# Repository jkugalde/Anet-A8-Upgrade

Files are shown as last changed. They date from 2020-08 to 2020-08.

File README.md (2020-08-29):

# Anet A8 Upgrade

I have an Anet A8, it was the cheapest 3d printer in the market around the time that i bought it (2019) and served its purpose well enough, but now with the pandemic lockdown i have enough time to invest in get some major upgrades done. 

This is a work in progress and i currently have only modified the frame, from acrylic to aluminium. I am planning to change the controller to one of the latest with touch screen compatibility, to make and enclosure to reduce heat dissipation and noise and maybe modify the mechanical arrangement to a corexy or something like that.

This is what i currently have:

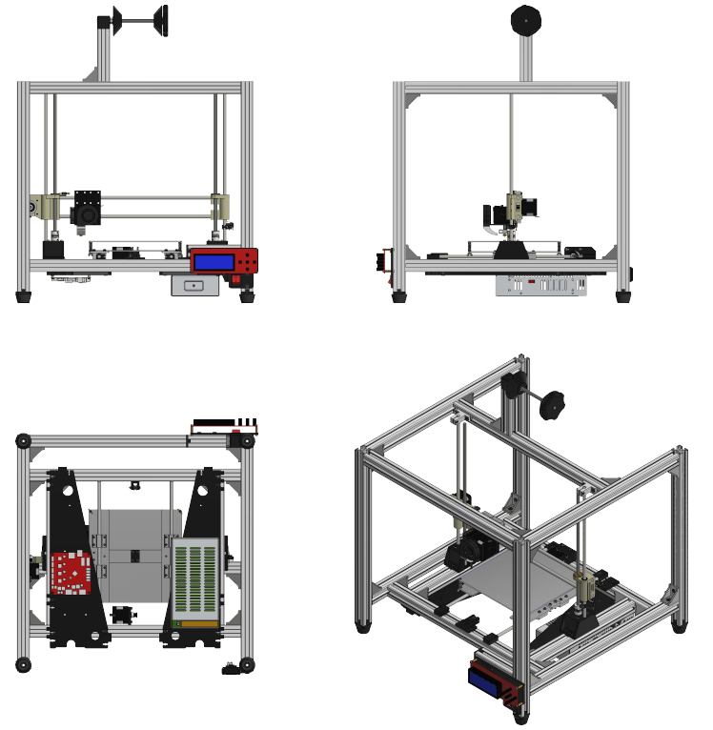
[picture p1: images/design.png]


# Design

The first objective in the project is to build a stiffer frame that is easy to enclose without invest too much time in making new parts to get the printer working, as it will be done anyway in the future when changing the controller and mechanical principle. 

## Aluminium frame

One of the main weaknesses of the AnetA8 is the acrylyc frame, which is not rigid enough to withstand high speed/torque, brittle, and difficult to enclose. As i had a good time making a [table](https://github.com/jkugalde/T-Slot-Table) with T-Slots aluminium profiles i thought why not?.

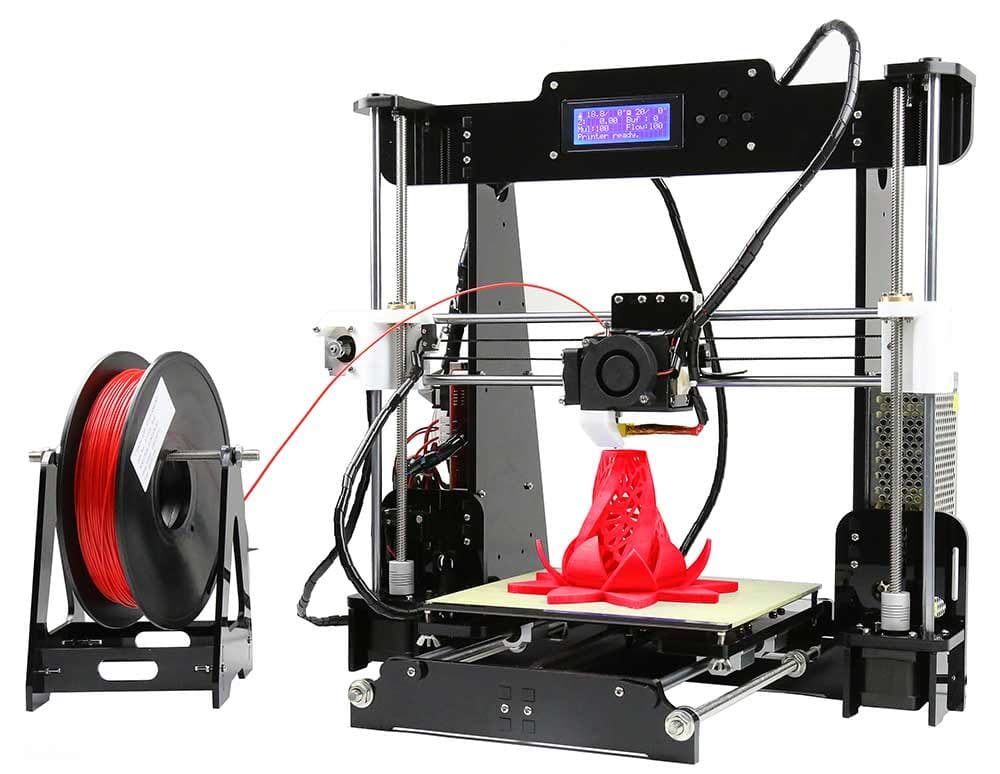
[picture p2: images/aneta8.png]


The criteria were:

- To make a box so it would be easier to build and enclose (probably more expensive tho).
- Big enough to fit the Anet parts.
- To use the profiles without cutting them.

I decided to use 30x30 T-Slots as they are cheaper and stronger than 20x20 V-Slots, which are also a good option to make machines too as there are plenty of accesories and also works as transmission system, but i am not going to make any changes in that last topic yet.

As the beams are sold in multiples of 250 mm and the Anet axis are longer than that i chose to use 500 mm profiles in the following design:

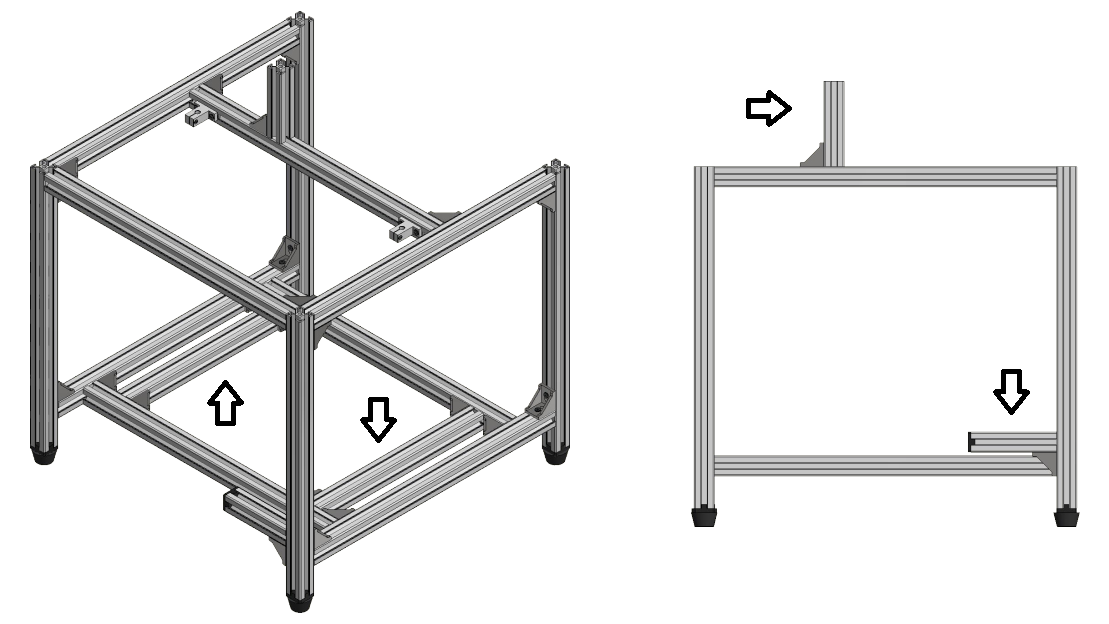
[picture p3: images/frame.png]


There is some space in the bottom to separate the electronics and power from the rest of the machine, wich will be in an enclosure in the future. The joints are corner brackets, you can add more or other type of joints to increase stiffness, i used the minimum as the enclosure will also help. The z axis rods are held by SK vertical supports. Unfortunately, there are four of the beams that must be cut to a different length, one of them is to hold the spool, other one for the screen, and the other two will support the z motors and define the length of the y axis. 

I could have made the y axis longer by simply not cutting these pair of profiles, but then i will have to buy new 8 mm steel rods, belt and bed system, so nah. I am planning to make a corexy anyway. Fortunately, i had a 1.5 m aluminium profile that i did not use in my table, so i cut it to make these beams and an extra 500 mm.

The foots are standard 30x30 T-Slot rubber foots with a 3d printed piece for attachment to the beams.

Finally, these are the parts:

Item                     | Quantity
 ---------------------------   | ------------
T-Slot 30x30x500 mm | 12
T-Slot 30x30x340 mm | 2
T-SLot 30x30x120 mm | 2
SK8 shaft support seat | 2
Corner bracket | 22
Rubber foots | 4
End Cap foot attachment | 5

NOTE1: The extra printed attachment is to cover the sharp corners of the aluminium profile that hols the screen.

NOTE2: The small beams could be smaller, like 3 cm smaller.

NOTE3: That extra beam for the LCD is temporal, as it will be held by the enclosure in the future.

## 3D Printed parts

As i dispose of the acrylyc frame, i had to design and print parts to hold and support some components. The idea was to make them small as possible until i get the printer working. The printed components are:

Item                     | Quantity
 ---------------------------   | ------------
Spool holder joint | 1
Spool holder nut hanlde | 1
Spool holder cone | 2
Y Axis rod holder A  | 2
Y Axis rod holder B  | 2
Y Axis pulley support | 1
Z Motor holder | 2
Y Motor holder  | 1
Z Endstop mount   | 1
Y Endstop mount   | 1
X Belt attachment| 2
Y Belt attachment A  | 1
Y Belt attachment B  | 1
Rocker Switch mount | 1
Power inlet mount | 1

The x belt attachments were made as the previous system (bolts and zip ties) is awful, these are not too fancy either, but will stand long enough until i change the extruder for something else.

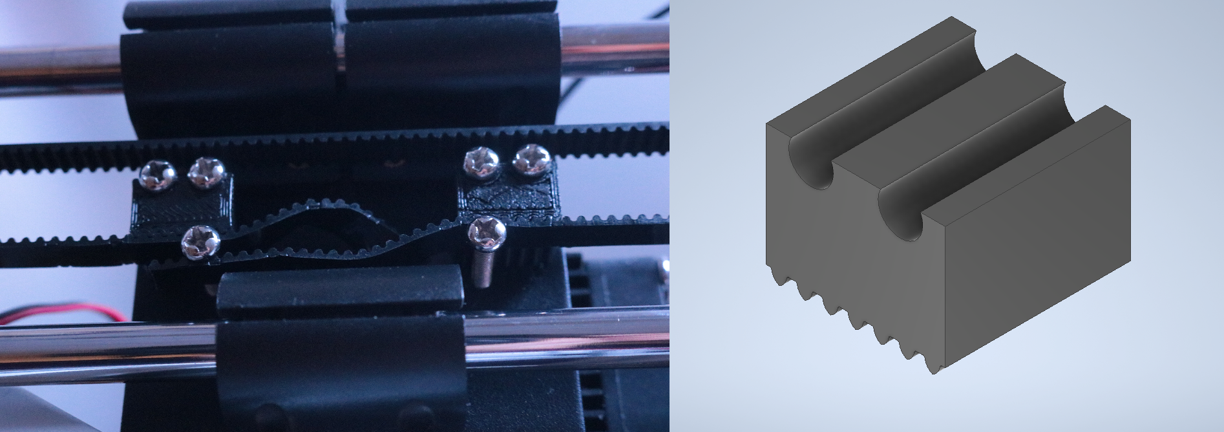
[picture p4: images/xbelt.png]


The y belt attachments were made as the height of the belt with respect to the y carriage changed. 

The other parts of the spool holder are on my [Thingiverse](https://www.thingiverse.com/thing:3457712), aswell as in this repository, except for the piece that joint the spool holder with the frame.

## Electronics

To hold the electronics the idea is to add a sheet of acrylic with mounting holes in the bottom face of the frame, but that will be done with the rest of the enclosure, so for now i will use the original parts of the anet where the electronics is mounted on, which attach really fine to the T-Slots and make everything easier, except for the inaccesibility of the SD port... well, is not difficult to make new holes to put the board closer to the edge or just USB print meanwhile.

I also reused one of the acrylic panels to hold the LCD.

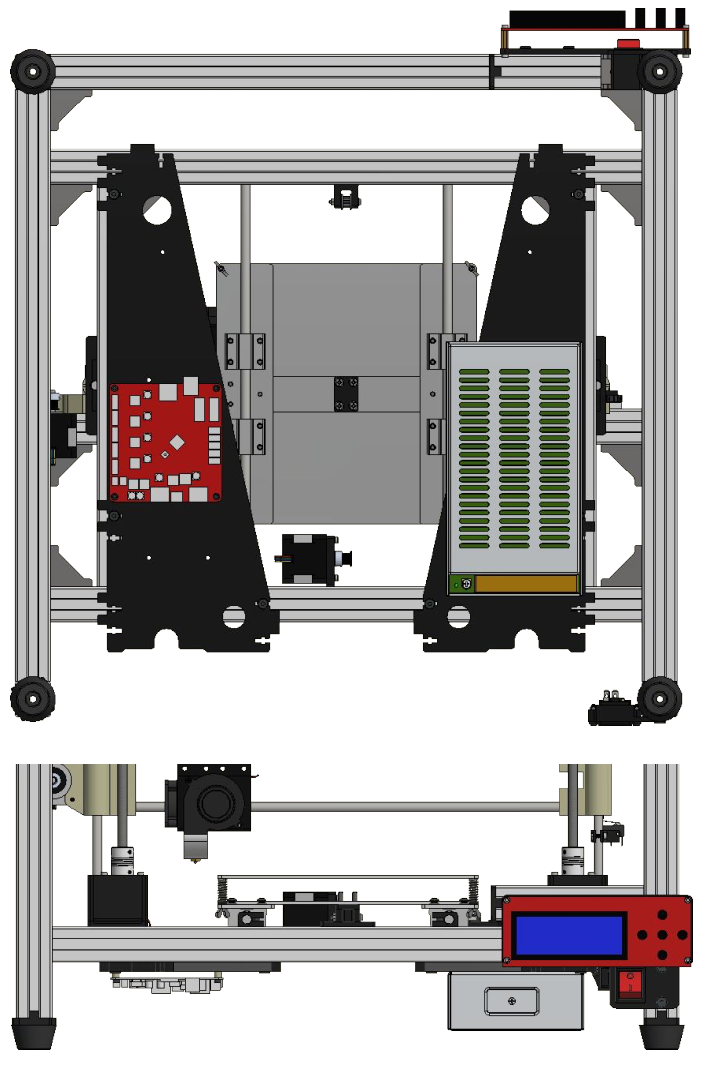
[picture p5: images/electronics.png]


# Manufacturing

## Disassembly

All the acrylyc frame was dispossed with the exception of the panels mentioned before.

All the other important parts were used, but the bearings that tightens the y belt were replaced with a proper GT2-16 idle pulley, which is also a good idea for the x belt, but there is not enough room.

## Cutting the profiles

I cut the 1.5 m profile with saw and then rectified the faces using a Tormach. The length has to be as accurate as possible and the faces must be flat to get a decent joint.

## Printing

All the part were printed with 0.3 mm layer height, 3 shells and 30% infill, no support nor raft, with exception of the z motor holders. These are the orientations:

Drill bits with the right dimensions were passed through all the holes in the pieces once they were printed, to clean.

## Extending wires

Some of the wires had to be extended due to the new position of the controller, these were:

- X endstop
- Extruder motor, fans, thermistor, heat cartridge
- Z endstop.

I had a power socket previously installed in the printer with a rocker switch, if you want to do this you will have to wire it like this:

(image)

# Assembly

## Frame

To assemble the profiles it is necessary to have a good square set and flat surfaces to get the joints perpendicular. 

- The first step is to attach the corner brackets (not too tight until the end) into every profile with bolts (M5x12) and nuts, you can use other profiles to help you with. 

- Then, assemble the "sides"

- The inside. Use a caliper to get the distances right.

- Put the sides in the inside.

- The upper profiles.

- Finally, the spool holder, but you can put it after all the other steps so it doesnt bother when wiring.

Be sure that the bolts are tight.

## Y Axis

- The motor in its holder then into the frame. Attach the motor loosely to then use the slotholes to tighten the belt.

- The pulley support.

- Put the shafts in the bed carriage and then into the rod holders. 

- This assembly into the frame.

- The y endstop support.

- The belt in the attachment and around the pulleys, and then tighten with the motor holder slotholes.

## X Axis

- The belt attachments and bolt (loosely).

- The shafts faces must be aligned with this side of the right support.

- Put the belt through the bearings, the motor, and then into the attachments. Fasten the bolt.

## Z Axis

- Put the motors (with the couple) in the holders, also bolts and nuts to attach to the profile.

- Pass the shafts and ACME thread through the bearings and nut.

- Put the assembly on the motors, fasten the set screw on the couples.

- Attach the SK8 to the shafts and frame.

- Attach the z endstop support (loosely).

To align the x axis, you can move the gantry all the way up in the z axis and compare the amount of ACME thread coming up from the nut and adjust.

## Electronics

- Use M3 bolts to attach the power source to one of the large acrylic panels, put M5x8 bolts and nuts in the indicated positions (yes, they fit right in).

- Use M3 bolts and nut and plastic separators to attach the motherboard to the other acrylic panel. Put the M5 bolts in the same positions as the previous step.

- Attach them to the frame.

- Connect everything as it was.

The wires were wrapped around with spiral wire wrap tube.

## Done(?)

Remember to level the bed. In my printer i also have a glass bed from an Ender3.

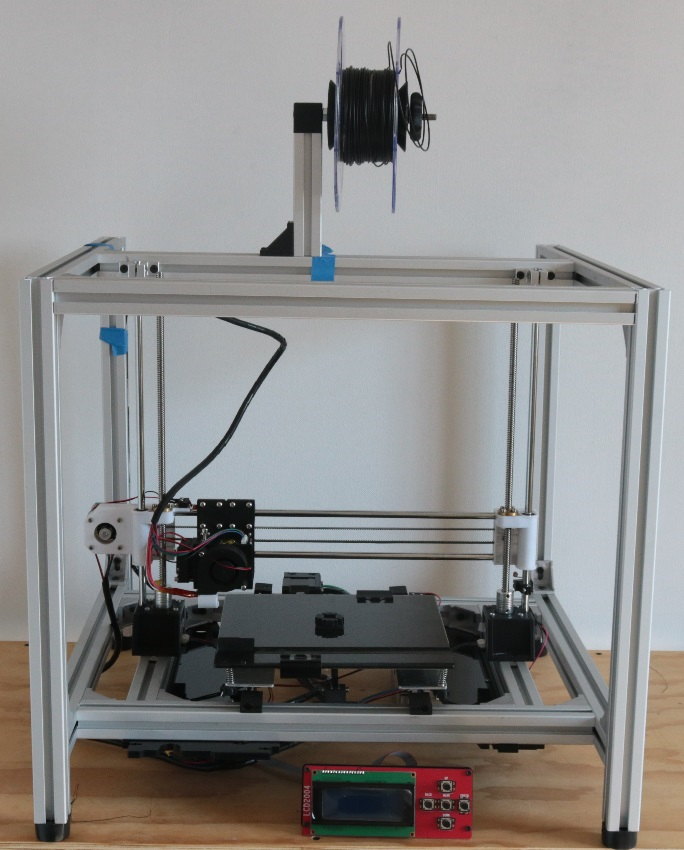
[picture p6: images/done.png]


# Further work

- Change the controller
- Build the enclosure
- Change the mechanical principle

With the current setting the usable printing area will 250x210 mm (X x Y) so it is a good idea to get a borosilicate glass bed to attach (remember to use only three bolts in the bed). There is a loss of Y space as i put the glass bed with metal clips, also because of the design, with other configuration you could get an extra 5-6 centimeters without the bed crashing into the enclosure.

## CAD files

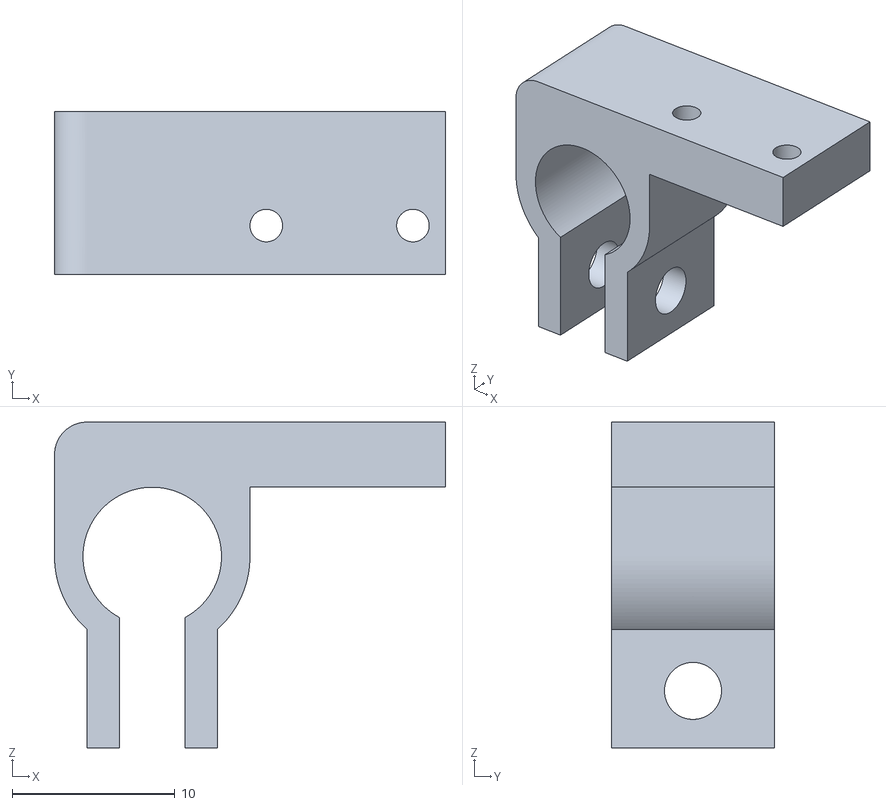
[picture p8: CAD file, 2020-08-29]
STLS/ZEndstopMount.stl
24.0 x 10.0 x 20.0

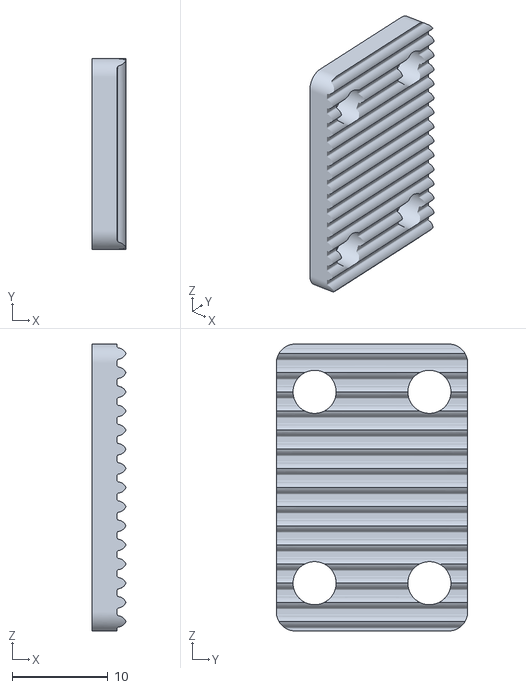
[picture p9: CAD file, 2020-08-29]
STLS/Y belt attachment B.stl
3.55 x 20.0 x 30.0

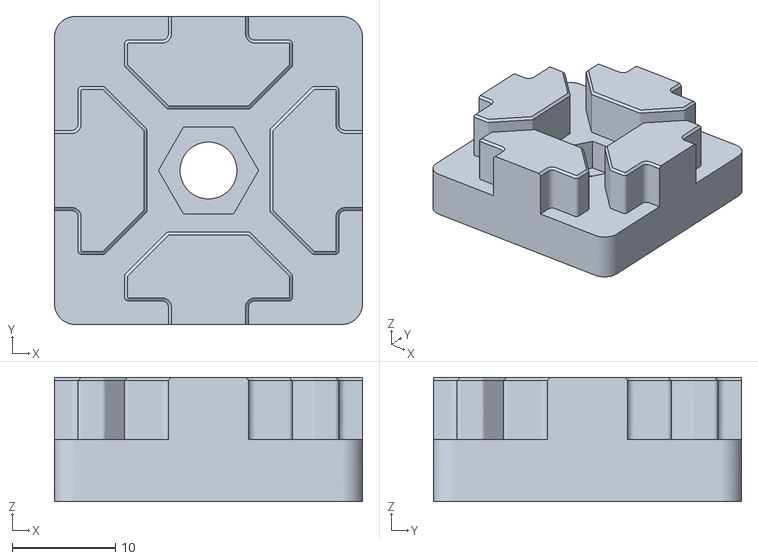
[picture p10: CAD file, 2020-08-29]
STLS/EndCapFoot.stl
29.8 x 29.8 x 12.0

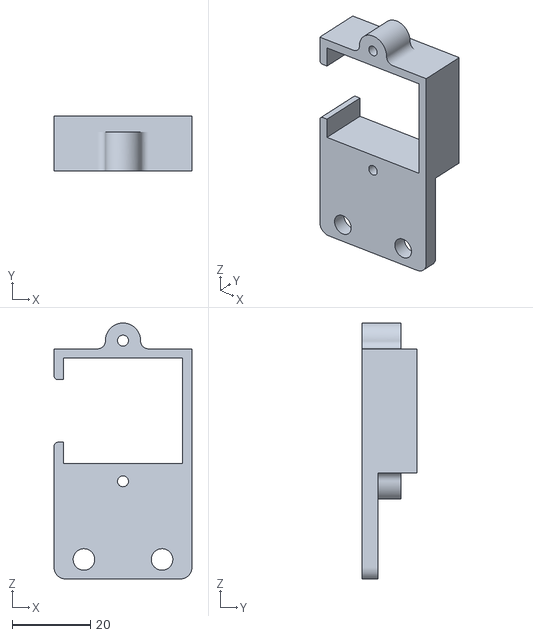
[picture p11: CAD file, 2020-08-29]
STLS/SocketMount.stl
35.3 x 14.0 x 65.5

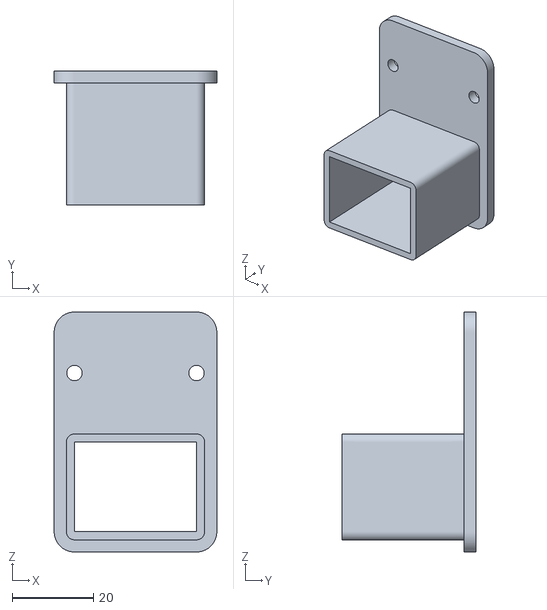
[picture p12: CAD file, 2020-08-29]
STLS/ButtonBox.stl
40.0 x 33.0 x 59.0

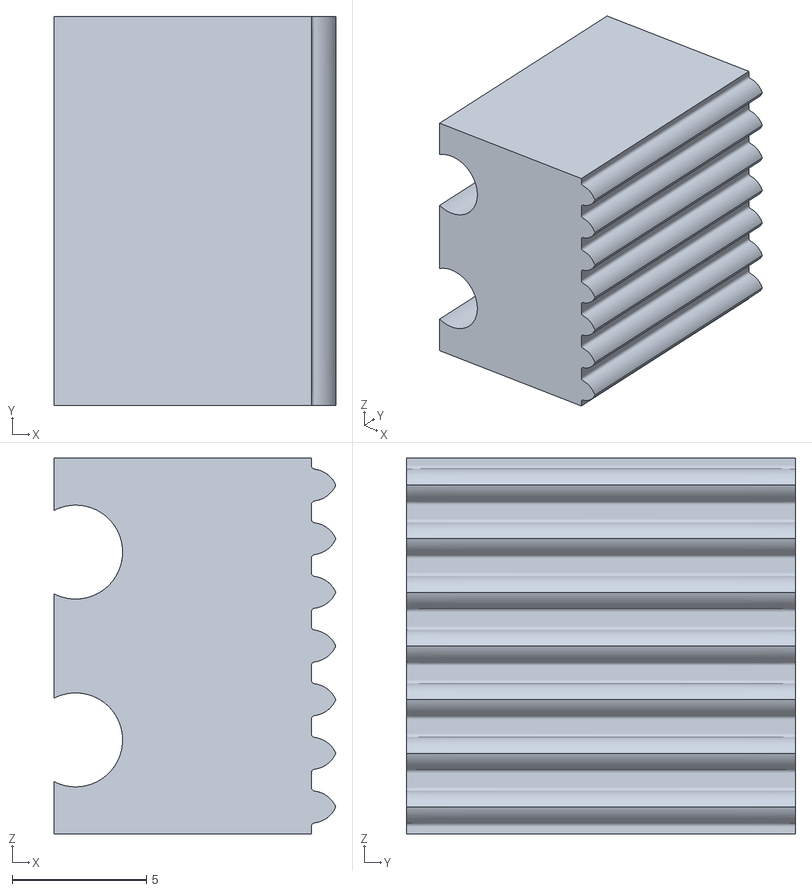
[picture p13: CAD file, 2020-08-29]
STLS/XBeltPress.stl
10.5 x 14.5 x 14.0

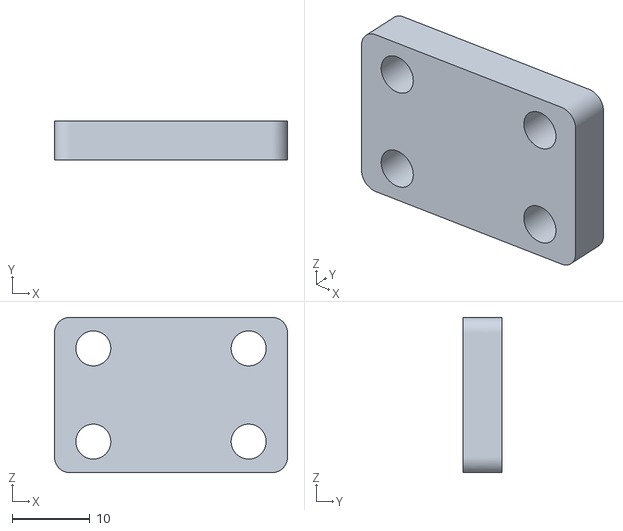
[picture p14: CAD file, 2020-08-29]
STLS/Y belt attachment A.stl
30.0 x 5.00 x 20.0

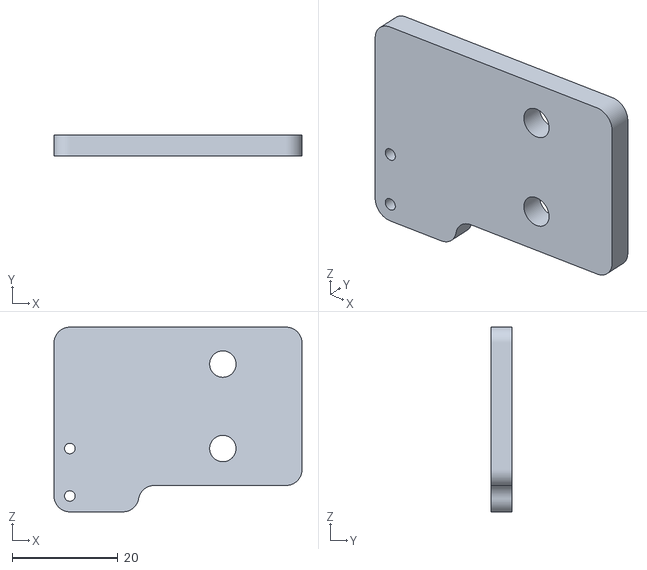
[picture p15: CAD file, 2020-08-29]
STLS/YEndstopMount.stl
47.0 x 4.00 x 35.0

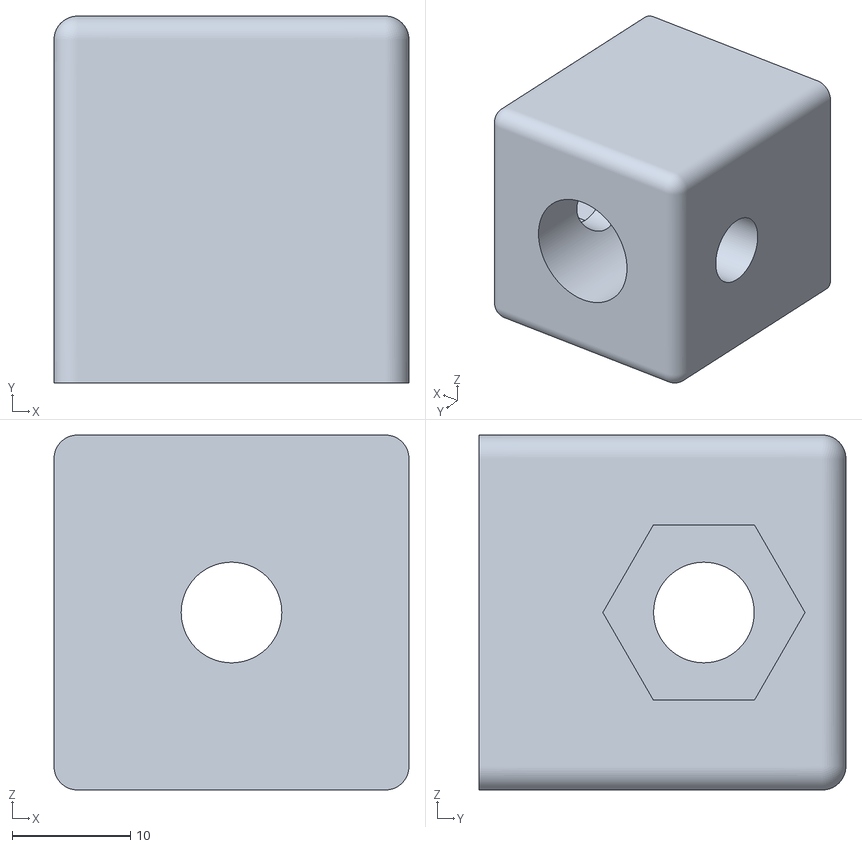
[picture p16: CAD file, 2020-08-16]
STLS/SpoolHolderJoint.stl
30.0 x 31.0 x 30.0

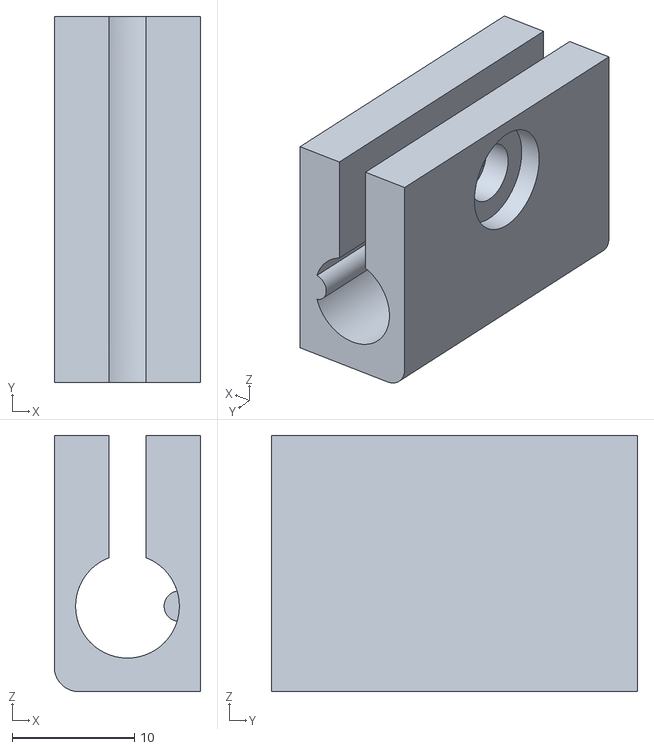
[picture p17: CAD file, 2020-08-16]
STLS/YsupportA.stl
12.0 x 30.0 x 21.0

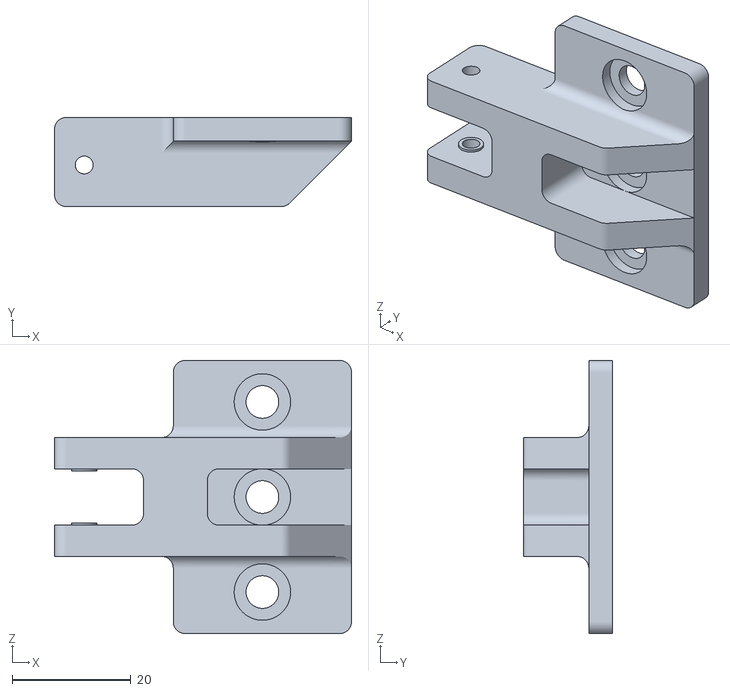
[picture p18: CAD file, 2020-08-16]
STLS/PulleySupport.stl
50.0 x 15.0 x 46.0

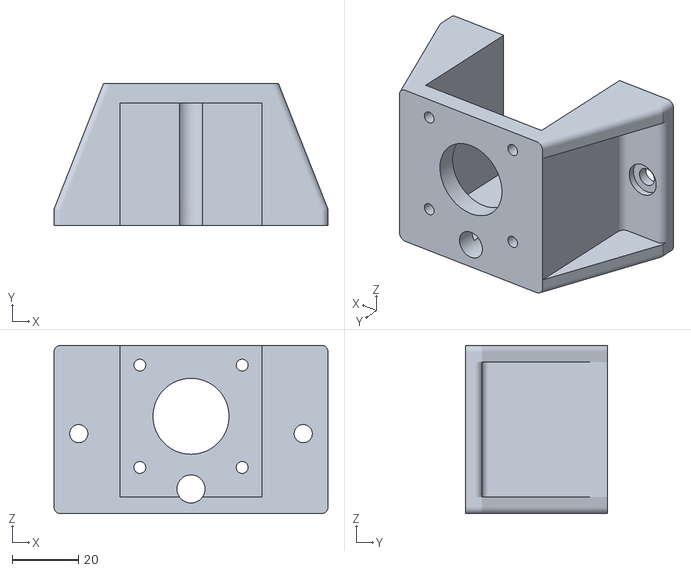
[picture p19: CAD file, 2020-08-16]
STLS/ZMotorSupport.stl
83.0 x 43.1 x 51.0

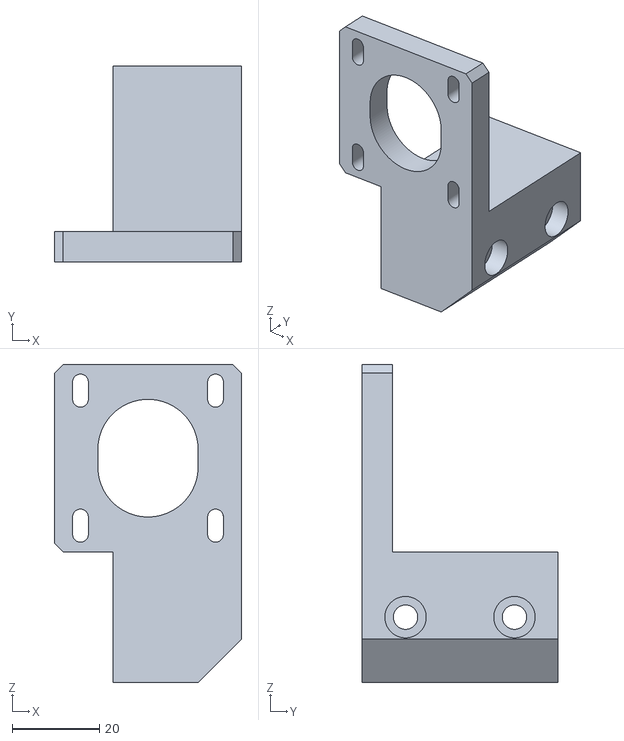
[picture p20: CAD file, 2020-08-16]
STLS/YMotorHolder.stl
43.0 x 45.0 x 73.0

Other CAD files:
STLS/YsupportB.stl
CAD/3030_endCap.ipt
CAD/3030cornerbracket.ipt
CAD/30x30x125.ipt
CAD/30x30x250.ipt
CAD/30x30x340.ipt
CAD/30x30x500.ipt
CAD/8x380axis.ipt
CAD/8x435axis.ipt
CAD/ACMENut.ipt
CAD/ACMEThread.ipt
CAD/AnetUpgrade.iam
CAD/Anet_A8_Main_Board_shell_v1.1.ipt
CAD/Bearing Ball, GT2 Timing Idler Pulley, Configurable_1 mm.ipt
CAD/Bearing Inner Ring, GT2 Timing Idler Pulley, Configurable_3 mm Bore, 6 mm OD.ipt
CAD/Bearing Outer Ring, GT2 Timing Idler Pulley, Configurable_3 mm Bore, 6 mm OD.ipt
CAD/Bearing Seal, GT2 Timing Idler Pulley, Configurable_3 mm Bore, 6 mm OD.ipt
CAD/Bearing Subassy, GT2 Timing Idler Pulley, Configurable_3 mm Bore, 6 mm OD.iam
CAD/Bearing608z.ipt
CAD/Bearingandbolts.iam
CAD/Bed.ipt
CAD/BedAssembly.iam
CAD/BedCarriageA.ipt
CAD/BedCarriageB.ipt
CAD/BedSpring.ipt
CAD/Bloqueo.ipt
CAD/BoardMount.iam
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
